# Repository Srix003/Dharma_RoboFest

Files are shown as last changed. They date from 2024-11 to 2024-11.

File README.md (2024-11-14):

# DHARMA BOT :dog2::robot:
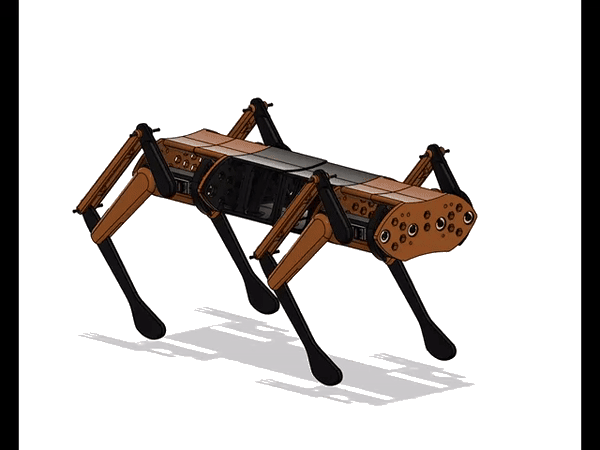
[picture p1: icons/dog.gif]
display_image


Dharma Bot is a sophisticated quadruped robotic dog featuring 12 degrees of freedom (DOF) for dynamic motion. The system includes a custom-designed remote control and smartwatch, which collectively offer seamless user interaction, control, and monitoring capabilities.

## Authors :writing_hand:

- [@mr-spaw](https://github.com/mr-spaw) :space_invader:
- [@LordCretivo](https://github.com/LordCretivo) :teddy_bear:
- [@DeepseaBandit](https://github.com/DeepseaBandit) :merman:

## Documentation :notebook_with_decorative_cover:

[Documentation](https://docs.google.com/document/d/14A3U6bSW9qBQt6sxEBGoiQTC8-wSntHT5azrs7TC3jw/edit?usp=sharing)

## System Overview :joystick: 
Dharma Bot is composed of three primary, electronically independent subsystems:
1. **The Bot**: The robotic dog, with core control and motion capabilities.
2. **Smart Remote**: The main control interface for the bot, featuring a Raspberry Pi, touchscreen, and long-range communication.
3. **Smartwatch**: A peripheral control and monitoring device equipped with sensors and ESP-32-based communications.
4. **Turret System**: The turret system is a rotating module mounted on the bot, designed to carry cameras and sensors. It provides 360-degree horizontal rotation and adjustable vertical tilt, enabling the bot to monitor or track targets in multiple directions.

## Subsystems

### [Smart Watch](Firmware/Utility_Watch/watch.md) :watch:
The smartwatch incorporates:
- **ESP-32 WROOM microcontroller**:The SoC of the embedded hardware.
- **OLED screen**: Displays real-time status, bot location, connectivity, and enemy detection data.
- **Pulse-meter sensor** and **GPS**: For monitoring the wearer's health and position.
- **Geotagging**: Logs location of deployed tags for tracking.
- **Heartbeat Monitoring**: In "Military Mode," it locks if the wearer’s pulse reads zero for over 30 seconds.
- **FailSafe Mechanism**: Notifies the remote of the current location upon triggering specific emergency conditions.
- **ESP-NOW Communication**: Provides secure data exchange between the smartwatch and the smart remote.

### Smart Remote  :video_game:
Serving as the primary control hub, the smart remote includes:
- **Raspberry Pi and 7-inch HDMI Touchscreen**: For intuitive control of the whole system architecture.
- **LoRa and ESP-NOW Modules**: Enabling long-range communication up to 10 km in LoRA and about five meters of communication with ESP-NOW protocol
- **GeoTag Integration**: Displays tagged locations on a map for rescue and tracking.
- **Video Streaming**: ESP-32 S3 CAM streaming for real-time surveillance.
- **Manual Controls**: Joysticks, potentiometers, and switches for bot locomotion and firing systems.
- **GUI**: The remote’s GUI interface provides a user-friendly experience, offering control over various modes, video feeds, and sensor data

### PoC Bot :dog2:
The main bot integrates:
- **Teensy 4.1 Microcontroller**: Manages core functions, including servo control and scheduling of Tasks
- **ESP 32 S3 Development Board**: Controlling the Peripheral Electronics like GPS, ToF Sensors and Gyroscopic Readngs.
- **MG99R Servo Motors**: 12 servo motors for precise locomotion.
- **ESP-32 S3 Camera System**: A esp camera system for live video feed.
- **LIDAR and GPS Modules**: For navigation and environmental awareness.
- **Communication**:  Local esp aceess network and long-range LoRa for data exchange between subsystems.

### Turret System :gun:
The turrent has:
- **Raspberry Pi**: Runs a local ML image recognition model and manages peripheral hardware.
- **ESP 32**: Controls the Servo motors

## Installation-Arduino IDE :computer:

### Ubuntu-linux64

Update Packages

```bash
sudo apt update
sudo apt upgrade
```

Installing Dependencies
```bash
sudo apt install -y wget unzip
```

Download the Arduino IDE
```bash
wget https://downloads.arduino.cc/arduino-<version>-linux64.tar.xz
```

Extract the Archive
```bash
tar -xf arduino-<version>-linux64.tar.xz
```

Install the Arduino IDE
```bash
cd arduino-<version>
sudo ./install.sh
```

Download the Arduino IDE
```bash
sudo usermod -aG dialout $USER
```

Launch Arduino IDE from Application menu or
[Arduino](https://www.arduino.cc/en/software)

then,
Go to File > Preferences (or Arduino > Preferences on macOS).
In the Preferences window, look for the field labeled Additional Board Manager URLs.
Paste the URLs for any additional board packages

```bash
http://arduino.esp8266.com/stable/package_esp8266com_index.json
https://github.com/earlephilhower/arduino-pico/releases/download/global/package_rp2040_index.json
https://raw.githubusercontent.com/espressif/arduino-esp32/gh-pages/package_esp32_index.json
https://www.pjrc.com/teensy/package_teensy_index.json
```
Go to Tools > Board > Board Manager.
Download ESP and Raspberry Pi Pico Board libraries
## 
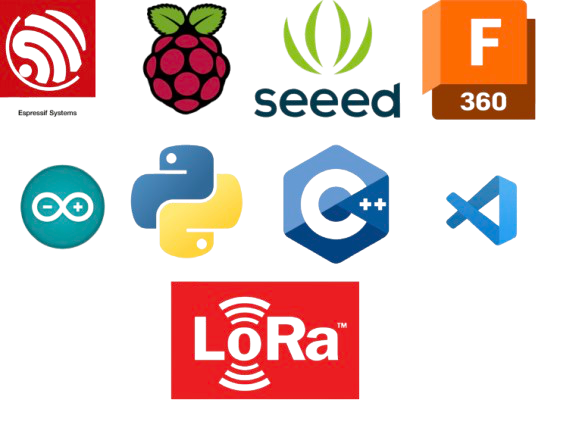
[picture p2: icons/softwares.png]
software_used


## Project Context :star: :india:
This project was developed as part of RoboFest, held in 2024, organised by Gujarat Council on Science and Technology(GUJCOST).

## Social Media :star2:
[Website](https://krs.kiit.ac.in)
[Instagram](https://www.instagram.com/kiit_robotics.society?utm_source=ig_web_button_share_sheet&igsh=ZDNlZDc0MzIxNw==)
[Linkedin](https://www.linkedin.com/company/kiit-robotics-society-bbsr/mycompany/)

## Project Link :link:
https://github.com/mr-spaw/Dharma_RoboFest

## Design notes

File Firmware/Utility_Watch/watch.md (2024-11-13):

# UTILITY WATCH :watch:

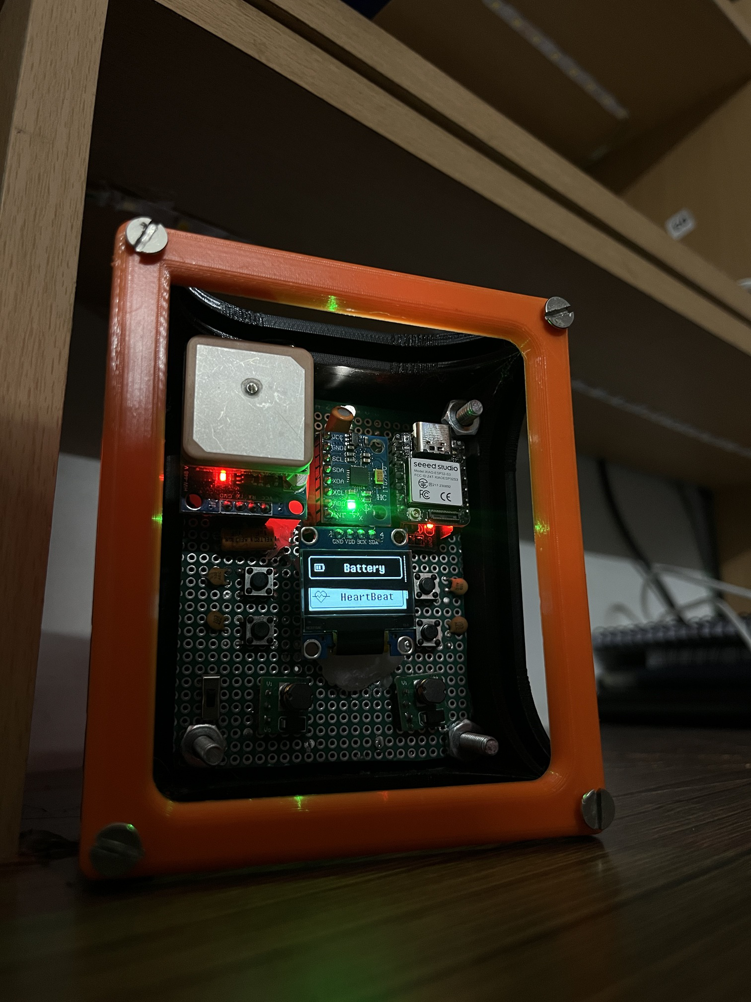
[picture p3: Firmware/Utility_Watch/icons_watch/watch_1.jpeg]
display_image


## Overview :eye_speech_bubble:

The Utility Watch is an embedded device designed to monitor health and environmental parameters using sensors. It includes features like heart rate monitoring, GPS tracking, and motion detection, with wireless data transmission through ESP-NOW. The watch has an OLED display for real-time data visualization and user interaction via buttons. In failsafe mode, if no motion or heart rate is detected, the watch disables user controls and only transmits essential data: heart rate and GPS location.

## Key Features :speech_balloon:

1. **Heart Rate Monitoring**: Utilizes the MAX30102 sensor to measure heart rate and SpO2 levels.

2. **GPS Tracking**: Retrieves geographical coordinates and satellite information using a GPS module.

3. **Motion Detection**: Employs the MPU6050 sensor to monitor motion and orientation.

4. **User Interface**: An OLED display provides graphical and textual feedback.
Users can navigate through different modes using buttons (up, down, select, and press).

5. **Failsafe Mode**: Activates when no motion or heart rate is detected. In this mode, the watch deactivates non-essential functions, rendering the buttons inactive. Only critical data, such as heart rate vitals and GPS location, is transmitted wirelessly.

## Components :play_or_pause_button:
**Microcontroller**: SEEDSTUDIO ESP32 S3

### Communication
ESP-NOW for wireless data transmission

### Sensors
1. **MPU6050**: Accelerometer and Gyroscope

2. **MAX30102**: Pulse Oximeter and Heart Rate Sensor

3. **NEO-7M**: Serial communication for location tracking

4. **OLED 0.96inch Display**: To dislplay the GUI of the watch

## RTOS Task Scheduling  :grey_exclamation:

### Task Breakdown

1. **Hardware Interrupts**: Handles button presses for user interaction.

2. **Sensor Data Acquisition**: Reads data from the MPU6050, MAX30102, and GPS.

3. **Data Preparation ESP-NOW**: Formats sensor data into a string for transmission.

4. **Data Transmission ESP-NOW**: Sends prepared data using ESP-NOW.

5. **OLED GUI Handling**: Updates the display based on user inputs and sensor readings.

6. **Data Retrieval ESP-NOW**: A preemptive task to manage background operations.

7. **FailSafe Mechanism**: Monitors sensor stability and activates failsafe mode if necessary.

8. **FailSafe GUI**: Displays relevant information during failsafe mode.

## Dependencies
To deploy this project run

```bash
Wire.h
Adafruit_GFX.h
Adafruit_SSD1306.h
MPU6050.h
esp_now.h
WiFi.h
SoftwareSerial.h
TinyGPS.h
MAX30105.h
heartRate.h
```
## Pin Configuration :part_alternation_mark:

The Smart Utility Watch utilizes various sensors and components, each connected to specific pins on the ESP32 microcontroller. Below is the detailed pin configuration for each component:

### GPS Module
```bash
Vcc: Connect to 3.3V
Gnd: Connect to Ground
Tx: Connect to Digital Pin D3
Rx: Connect to Digital Pin D2
```

### MAX30102 (Heart Rate Sensor)
```bash
Vcc: Connect to 3.3V
Gnd: Connect to Ground
SDA: Connect to Digital Pin D4
SCL: Connect to Digital Pin D5
```

### MPU6050 (Accelerometer and Gyroscope)
```bash
Vcc: Connect to 3.3V
Gnd: Connect to Ground
SDA: Connect to Digital Pin D4
SCL: Connect to Digital Pin D5
```

### OLED Display (SSD1306)
```bash
Vcc: Connect to 3.3V
Gnd: Connect to Ground
SDA: Connect to Digital Pin D4
SCL: Connect to Digital Pin D5
```

### Buttons
```bash
Up Button: Connect to Digital Pin D10
Down Button: Connect to Digital Pin D9
Select Button: Connect to Digital Pin D8
Press Button: Connect to Digital Pin D0
```

### Voltage Divider for ADC
```bash
R1: 10K Ohm resistor
R2: 1K Ohm resistor
ADC: Connect to Digital Pin D1
```
#### Notes

1. Ensure that all components are connected correctly to prevent damage to the sensors or the microcontroller.
2. The power supply should be stable 3.3V to the ESP32 and provide sufficient current for all connected devices.
3. Decoupling Capacitor is necessary for the button to ensure reliable operation.

## GUI :open_file_folder:
The smartwatch begins by detecting the wrist; if no wrist is detected, it will not proceed. Once detected, it starts collecting data, and when the heartbeat exceeds 30 BPM, it transitions to the main interface. The most recent GPS, MPU, and heart rate data are stored in a linked list with the newest entry at the top and the oldest at the bottom.

The main interface has four sections. 

The main interface is divided into four sections:

1. **Enemy Section**: Displays the watch’s mode and the remote dog's mode—Sentry mode, Scout mode, and Follow mode—and shows any enemy detected by the bot.
2. **GPS Section**: Shows the device's current latitude, longitude, and the number of connected satellites.
3. **Battery Section**: Indicates the battery levels of the smartwatch, the remote, and the POC bot.
4. **Heart Vitals Section**: Displays the user’s current BPM and average BPM readings.

### Failsafe Mechanism
The FailSafe Mechanism, begins by collecting pitch, roll, and yaw values from the first node, then compares these values to nodes 2 through 5 to check for stability within a defined tolerance. If all nodes are stable and the average BPM of the first node is below 25, it activates the failsafe mode. This triggers specific safety actions, such as calling task3 and task4 and setting a failsafe_bool flag to indicate that failsafe mode is active.

## Conclusion

The Smart Utility Watch is a versatile device that combines health monitoring and GPS functionalities in a compact form factor. Its modular design allows for easy updates and improvements, making it a suitable project for both hobbyists and developers interested in wearable technology.

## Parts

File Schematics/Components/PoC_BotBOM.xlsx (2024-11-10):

Components | Quantity | Price | Total Price | Link
Teensy 4.1 Dev-Board | 1 | 2658 | 2658 | https://robu.in/product/buy-teensy-4-1-development-board/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
ESP 32 S3 Dev-Board | 1 | 1388 | 1388 | https://robu.in/product/smartelex-esp32-s3-development-kit-m-1-1-pcs/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
Seedstudio XIAO ESP-S3 Cam | 1 | 1300 | 1300 | https://www.digikey.in/en/products/detail/seeed-technology-co.,-ltd/113991115/18724504?cur=INR&lang=en&gad_source=1&gbraid=0AAAAADrbLlhHJjHy-7D3tAoVhXMwgyvdG
SX1278 LoRa Module | 1 | 430 | 430 | https://robocraze.com/products/sx1278-lora-module-ra-02-433mhz-wireless-spread-spectrum-transmission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
GY-91 10 DOF IMU MPU-9250 with BMP280 | 1 | 590 | 590 | https://robu.in/product/gy-91-mpu9250bmp280-10dof-acceleration-gyro-9-axis-sensor-module/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
VL53LoX ToF Sensor | 4 | 111 | 444 | https://robu.in/product/vl53l0x-tof-based-lidar-laser-distance-sensor/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
NEO 7M GPS Module | 1 | 545 | 545 | https://robu.in/product/neo-7m-000-neo-7m-gps-module-mwc-gy-neo-7m-v2-flight-control-gps-module-eeprom-mwc-apm2-5/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
1.3 inch OLED Display | 1 | 350 | 350 | https://zbotic.in/product/1-3-inch-i2c-iic-4-pin-oled-display-module-with-vcc-gnd-blue/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
MG996R Servo Motor | 12 | 309 | 3708 | https://robu.in/product/towerpro-mg995-servo-high-speed-digital-metal-gear-ball-bearing-torque-12kg-robot-arduino-good-quality180-degree-rotation/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
AMS1117 3.3V Module | 3 | 18 | 54 | https://robu.in/product/ams1117-3-3-ldo-800ma-dc-5v-3-3v-step-power-supply-module/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
USB Buck Converter | 2 | 80 | 160 | https://robu.in/product/usb-fast-charging-module/?gad_source=1&gbraid=0AAAAADvLFWfHbZ1aIqX8F5rfsQEMRjSHD
XT-60 Connector | 2 | 26 | 52 | https://robocraze.com/products/xt60-connector-pair?currency=INR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
4s Battery | 1 | 1869 | 1869 | https://robu.in/product/orange-2200mah-4s-40c80c-lithium-polymer-battery-pack-lipo/
VeroBoard | 6 | 94 | 564 | https://robu.in/product/10-x-15-cm-universal-pcb-prototype-board-single-sided-2-54mm-hole-pitch/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
Silicon Wire 18 AWG | 4 | 60 | 240 | https://robu.in/product/high-quality-ultra-flexible-18awg-silicone-wire-red/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
JST-XT connectors 2 pin | 10 | 60 | 600 | https://robu.in/product/2-pin-jst-xh-2-54mm-pitch-plug-and-socket-with-cable-10-pcs/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
JST-XT connectors 4 pin | 15 | 50 | 750 | https://zbotic.in/product/6-pin-jst-xh-2-54mm-pitch-plug-and-socket-with-cable-3-pcs/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
PCT-SPL 2:6 | 2 | 66 | 132 | https://robu.in/product/pct-spl-62-0-08-2-5mm-62-pole-wire-connector-terminal-block-with-spring-lock-lever-for-cable-connection/
PCT-SPL 1:1 | 2 | 21 | 42 | https://robu.in/product/lt-211spl-1-quick-connection-terminals-can-be-spliced/
Silicon Wire 28 AWG | 4 | 60 | 240 | https://robu.in/product/28awg-silicone-wire/?gad_source=1&gbraid=0AAAAADvLFWeTgUz2OswCMdNMzaCTK1-p6
Total |  |  | 16116

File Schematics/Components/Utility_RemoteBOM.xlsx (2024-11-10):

Component | Quantity | Price | Total | Link
70H-1024600-IPS-Panel by Waveshare | 1 | 4649 | 4649.00 | https://thinkrobotics.com/products/7inch-qled-integrated-touch-display-1024-600?variant=46572922995005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
Raspberry Pi 5 4 GB | 1 | 5799 | 5799.00 | https://robu.in/product/raspberry-pi-5-model-4gb/
ESP 32 S3 Dev-Boards | 2 | 1388 | 2776.00 | https://robu.in/product/smartelex-esp32-s3-development-kit-m-1-1-pcs/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
ESP 32 Dev-Board | 1 | 420 | 420.00 | https://robocraze.com/products/nodemcu-32-wifi-bluetooth-esp32-development-board30-pin?variant=42268194046176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
SX1278 LoRa Module | 1 | 430 | 430.00 | https://robocraze.com/products/sx1278-lora-module-ra-02-433mhz-wireless-spread-spectrum-transmission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
3.7v Lithium Ion Batterys | 6 | 149 | 894.00 | https://robu.in/product/orange-icr-18650-2200mah-lithium-ion-battery/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
4s BMS Module | 1 | 160 | 160.00 | https://robu.in/product/4s-20a-lithium-battery-protection-board/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
4s Charger Module | 1 | 260 | 260.00 | https://robu.in/product/18650-polymer-lithium-ion-charger-type-c-to-4s-16-8v-4a-booster-module/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
AMS1117 3.3V modules | 3 | 18 | 54.00 | https://robu.in/product/ams1117-3-3-ldo-800ma-dc-5v-3-3v-step-power-supply-module/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
USB Buck converters 5V | 2 | 80 | 160.00 | https://robu.in/product/usb-fast-charging-module/?gad_source=1&gbraid=0AAAAADvLFWfHbZ1aIqX8F5rfsQEMRjSHD
2-axis Joysticks | 4 | 44 | 176.00 | https://robocraze.com/products/joystick-module?variant=40192421527705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
Switch | 2 | 16 | 32.00 | https://evelta.com/rocker-switch-on-off-spst-2pin-black-button-black-housing-kcd1-2-101/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
Toggle Switch | 3 | 30 | 90.00 | https://robu.in/product/smts-102-sub-miniature-toggle-switch-3pinon-on/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
Veroboard | 6 | 94 | 564.00 | https://robu.in/product/10-x-15-cm-universal-pcb-prototype-board-single-sided-2-54mm-hole-pitch/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
Silicon Wire 28 AWG | 6 | 60 | 360.00 | https://robu.in/product/28awg-silicone-wire/?gad_source=1&gbraid=0AAAAADvLFWeTgUz2OswCMdNMzaCTK1-p6
PCB power terminal | 15 | 10 | 150.00 | https://robu.in/product/2-pin-straight-pcb-screw-terminal-block-connector-3-5mm-pitch/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
5v Buck Converter | 2 | 100 | 200.00 | https://robu.in/product/ultra-small-size-dc-dc-5v-3a-bec-power-supply-buck-step-down-module/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
18650 Battery Holder | 5 | 83 | 415.00 | https://robu.in/product/18650-dual-smd-smt-high-quality-single-battery-holder/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
Silicon Wire 18 AWG | 3 | 60 | 180.00 | https://robu.in/product/high-quality-ultra-flexible-18awg-silicone-wire-red/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
JST-XT connectors 2 pin | 10 | 60 | 600.00 | https://robu.in/product/2-pin-jst-xh-2-54mm-pitch-plug-and-socket-with-cable-10-pcs/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
JST-XT connectors 4 pin | 30 | 50 | 1500.00 | https://zbotic.in/product/6-pin-jst-xh-2-54mm-pitch-plug-and-socket-with-cable-3-pcs/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
PCT-SPL 2:6 | 2 | 66 | 132.00 | https://robu.in/product/pct-spl-62-0-08-2-5mm-62-pole-wire-connector-terminal-block-with-spring-lock-lever-for-cable-connection/
PCT-SPL 1:1 | 4 | 21 | 84.00 | https://robu.in/product/lt-211spl-1-quick-connection-terminals-can-be-spliced/
5V to 3.3 Buck converter | 1 | 90 | 90.00 | https://robu.in/product/dc-dc-3a-5v-12v-24v-to-3-3v-step-down-power-supply-module/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
Total |  |  | 20175.00

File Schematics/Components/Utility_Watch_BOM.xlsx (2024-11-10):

Components | Quantity | PRICE | TOTAL | Link
GPS NEO 7M | 1 | 545 | 545 | https://robu.in/product/neo-7m-000-neo-7m-gps-module-mwc-gy-neo-7m-v2-flight-control-gps-module-eeprom-mwc-apm2-5/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
Seedstudio XIAO ESP S3 | 1 | 686 | 686 | https://robu.in/product/seeed-studio-xiao-esp32s3-2-4ghz-wifi-ble-5-0/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
MPU 6050 | 1 | 140 | 140 | https://robocraze.com/products/mpu-6050-triple-axis-accelerometer-gyroscope-module?variant=40192322011289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
0.96 inch OLED Screen | 1 | 140 | 140 | https://robocraze.com/products/0-96in-oled-display?variant=40192586645657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
Tactile buttons(pack of 20) | 1 | 59 | 59 | https://robu.in/product/6x6x5mm-tactile-push-button-switch-pack-of-20/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
TP4056 charging module | 1 | 17 | 17 | https://zbotic.in/product/tp4056-battery-charging-protection-module-type-c/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
3.7v Lithium Ion Battery | 1 | 200 | 200 | https://robu.in/product/450mah-pcm-protected-micro-li-po-battery/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
Vero Board | 1 | 85 | 85 | https://robu.in/product/9-x-15-cm-universal-pcb-prototype-board-single-sided-2-54mm-hole-pitch/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
3.3V to 5V boost converter | 2 | 48 | 96 | https://www.flyrobo.in/1.5v-1.8v-2.5v-3v-3.3v-3.7v-4.2v-5v-dc-dc-dc-boost-converter-step-up-module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
AMS1117 LDO | 2 | 18 | 36 | https://robu.in/product/ams1117-3-3-ldo-800ma-dc-5v-3-3v-step-power-supply-module/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
Silicon Wire 28 AWG | 2 | 60 | 120 | https://robu.in/product/28awg-silicone-wire/?gad_source=1&gbraid=0AAAAADvLFWeTgUz2OswCMdNMzaCTK1-p6
TOTAL |  |  | 2004

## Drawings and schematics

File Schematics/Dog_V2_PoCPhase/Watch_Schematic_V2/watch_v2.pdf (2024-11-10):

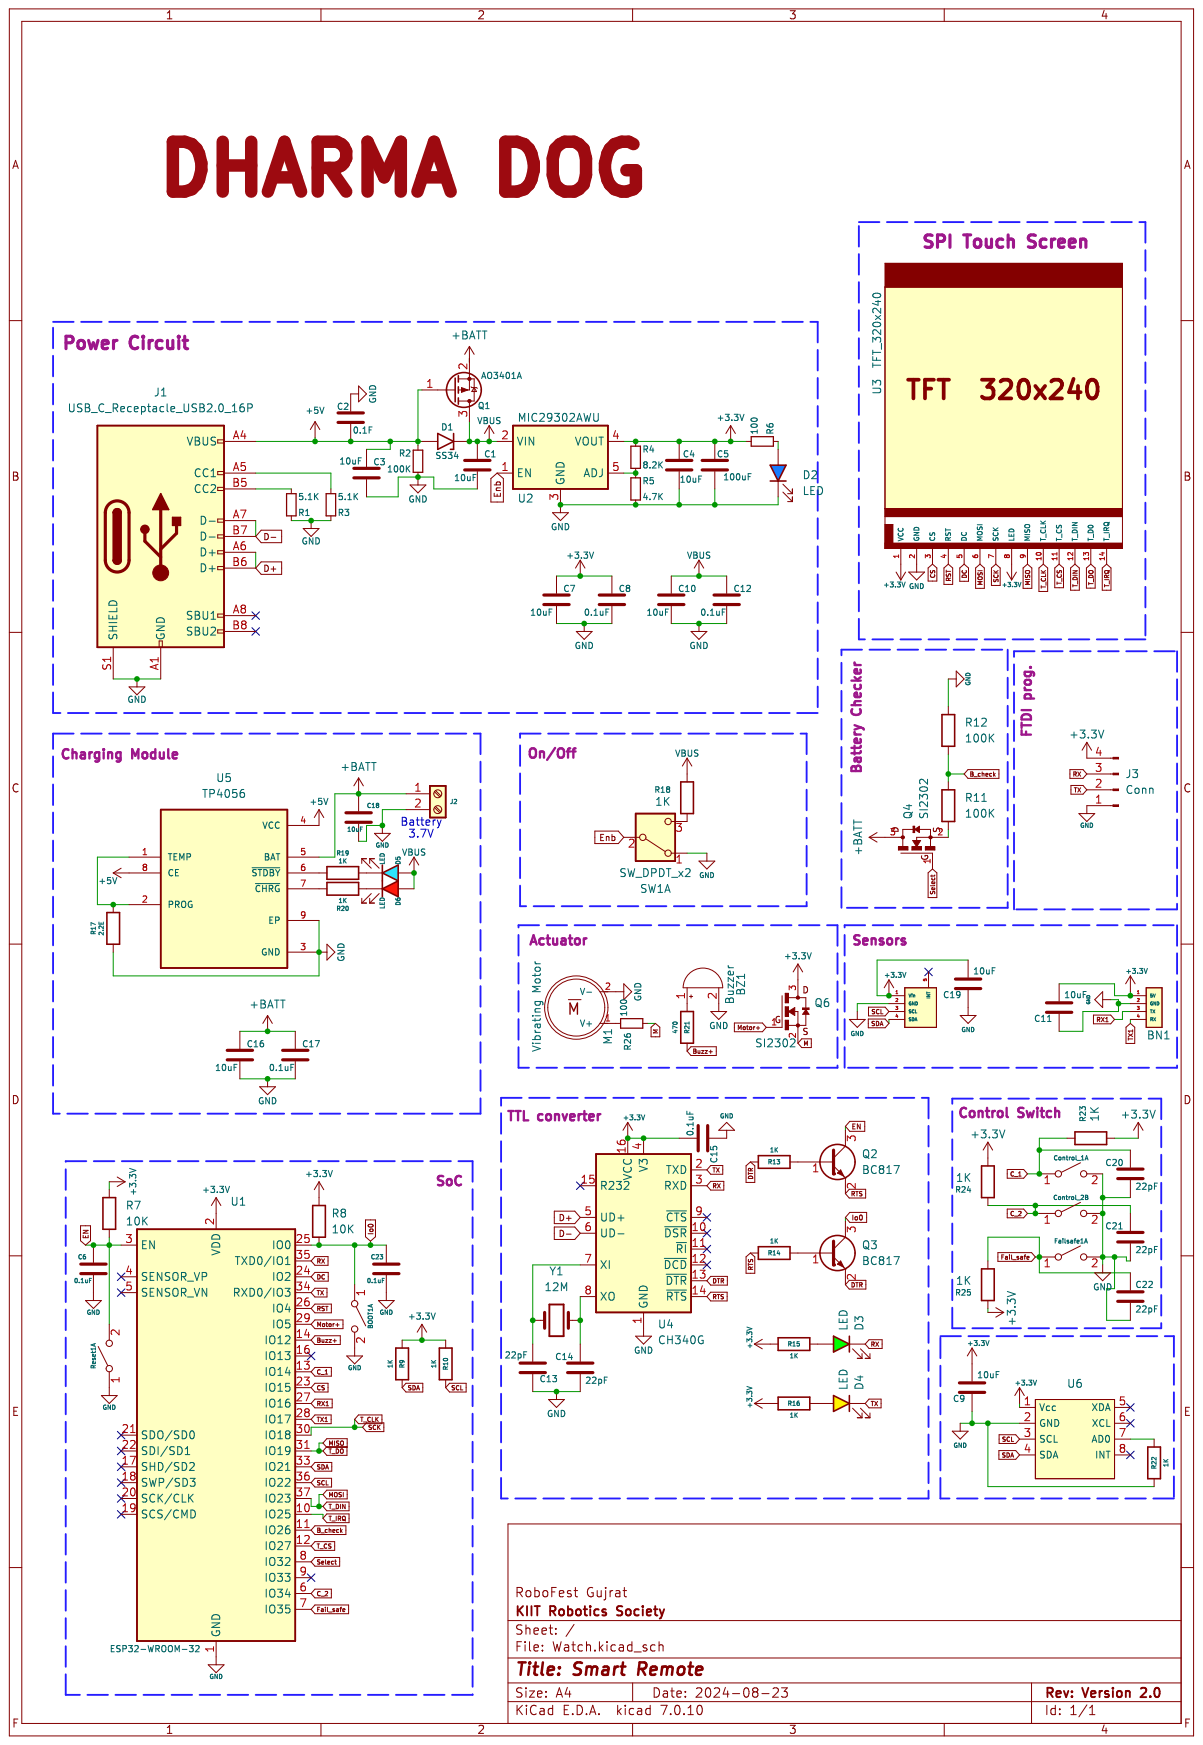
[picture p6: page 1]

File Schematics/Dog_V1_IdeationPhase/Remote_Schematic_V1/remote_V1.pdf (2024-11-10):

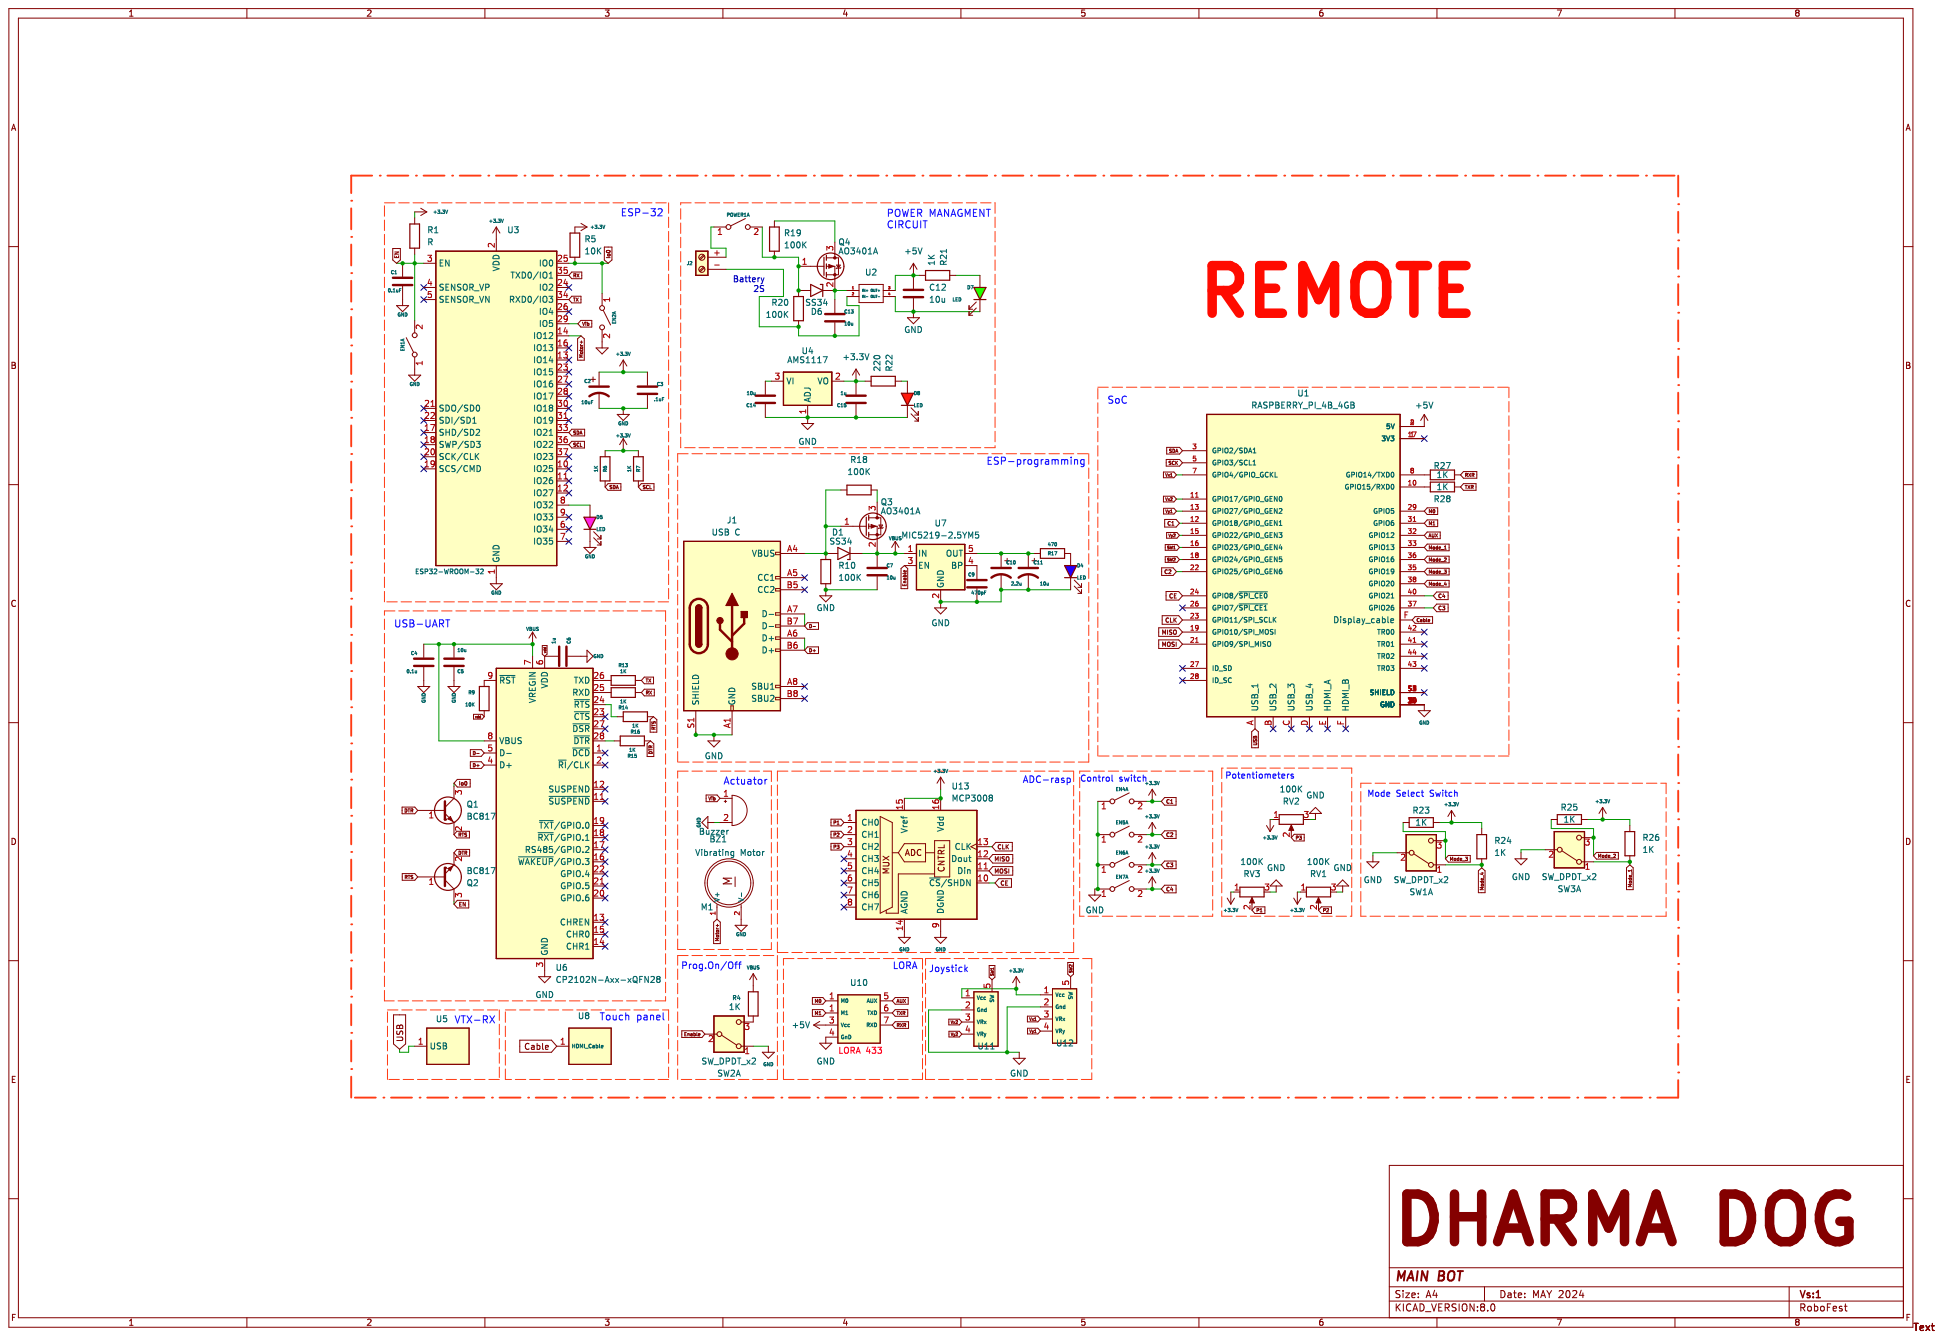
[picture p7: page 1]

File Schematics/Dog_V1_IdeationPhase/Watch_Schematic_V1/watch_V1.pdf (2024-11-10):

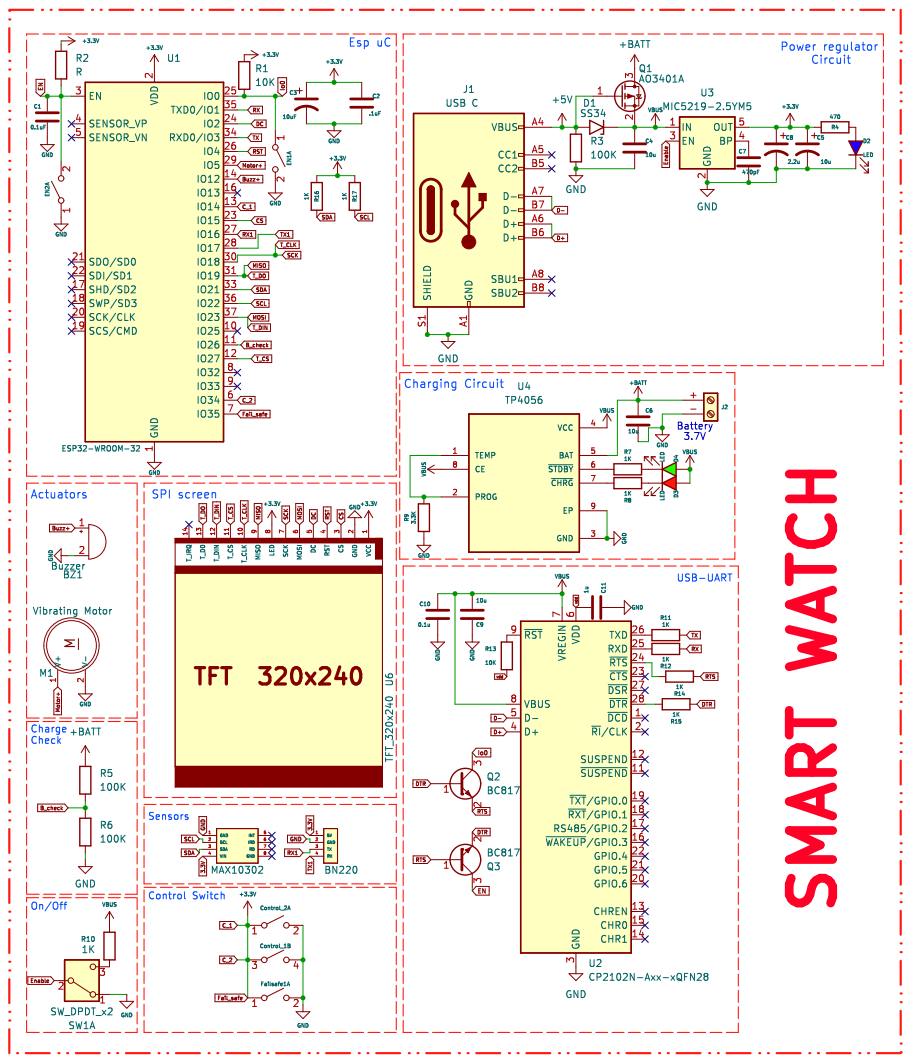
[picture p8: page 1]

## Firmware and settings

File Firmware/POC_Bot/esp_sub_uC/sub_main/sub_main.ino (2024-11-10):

#include <Wire.h>
#include <Adafruit_GFX.h>
#include <Adafruit_SH110X.h>
#include <SoftwareSerial.h> //softserail for UART
#include <TinyGPS.h>
#include <Adafruit_VL53L0X.h>
#include <MPU9250_asukiaaa.h>
#include <Adafruit_BMP280.h>
#include <freertos/FreeRTOS.h>
#include <freertos/task.h>
#include <freertos/semphr.h>

SemaphoreHandle_t xSemaphore;

#ifdef _ESP32_HAL_I2C_H_
#define SDA_PIN 6
#define SCL_PIN 7
#endif

#define i2c_Address 0x3c 
#define SLAVE_ADDR 0x78 
SoftwareSerial mySerial(41, 42);

#define SCREEN_WIDTH 128 
#define SCREEN_HEIGHT 64 
#define OLED_RESET -1
Adafruit_SH1106G display = Adafruit_SH1106G(SCREEN_WIDTH, SCREEN_HEIGHT, &Wire, OLED_RESET);


TinyGPS gps;

Adafruit_BMP280 bme;
MPU9250_asukiaaa mySensor;

float aX, aY, aZ, aSqrt, gX, gY, gZ;
float latitude, longitude;
int distance_sensor1;
int distance_sensor2;
int distance_sensor3;
int distance_sensor4;
String dist="";
int tol=100;


#define SENSOR1_WIRE Wire
#define SENSOR2_WIRE Wire
#define SENSOR3_WIRE Wire
#define SENSOR4_WIRE Wire

// Setup mode for doing reads
typedef enum {
  RUN_MODE_DEFAULT = 1,
  RUN_MODE_CONT
} runmode_t;

runmode_t run_mode = RUN_MODE_DEFAULT;
uint8_t show_command_list = 1;

typedef struct {
  Adafruit_VL53L0X *psensor; // pointer to object
  TwoWire *pwire;
  int id;            // id for the sensor
  int shutdown_pin;  // which pin for shutdown;
  Adafruit_VL53L0X::VL53L0X_Sense_config_t
      sensor_config;     // options for how to use the sensor
  uint16_t range;        // range value used in continuous mode stuff.
  uint8_t sensor_status; // status from last ranging in continuous.
} sensorList_t;

// Actual object, could probably include in structure above61
Adafruit_VL53L0X sensor1;
Adafruit_VL53L0X sensor2;
Adafruit_VL53L0X sensor3;
Adafruit_VL53L0X sensor4;

// Setup for 4 sensors
sensorList_t sensors[] = {
    {&sensor1, &SENSOR1_WIRE, 0x30, 10,
     Adafruit_VL53L0X::VL53L0X_SENSE_LONG_RANGE, 0, 0},
    {&sensor2, &SENSOR2_WIRE, 0x31, 11,
     Adafruit_VL53L0X::VL53L0X_SENSE_HIGH_SPEED, 0, 0},
    {&sensor3, &SENSOR3_WIRE, 0x32, 12,
     Adafruit_VL53L0X::VL53L0X_SENSE_DEFAULT, 0, 0},
    {&sensor4, &SENSOR4_WIRE, 0x33, 13,
     Adafruit_VL53L0X::VL53L0X_SENSE_DEFAULT, 0, 0}
};

const int COUNT_SENSORS = sizeof(sensors) / sizeof(sensors[0]);

const uint16_t ALL_SENSORS_PENDING = ((1 << COUNT_SENSORS) - 1);
uint16_t sensors_pending = ALL_SENSORS_PENDING;
uint32_t sensor_last_cycle_time;


void Initialize_sensors() {
  bool found_any_sensors = false;
  // Set all shutdown pins low to shutdown sensors
  for (int i = 0; i < COUNT_SENSORS; i++)
    digitalWrite(sensors[i].shutdown_pin, LOW);
  delay(10);

  for (int i = 0; i < COUNT_SENSORS; i++) {
    // one by one enable sensors and set their ID
    digitalWrite(sensors[i].shutdown_pin, HIGH);
    delay(10); // give time to wake up.
    if (sensors[i].psensor->begin(sensors[i].id, false, sensors[i].pwire,
                                  sensors[i].sensor_config)) {
      found_any_sensors = true;
    } else {
      Serial.print(i, DEC);
      Serial.print(F(": failed to start\n"));
    }
  }
  if (!found_any_sensors) {
    Serial.println("No valid sensors found");
    while (1)
      ;
  }
}
//====================================================================
// Simple Sync read sensors.
//====================================================================
void read_sensors() {
  // First use simple function
  uint16_t ranges_mm[COUNT_SENSORS];
  bool timeouts[COUNT_SENSORS];
  uint32_t stop_times[COUNT_SENSORS];

  digitalWrite(13, HIGH);
  uint32_t start_time = millis();
  for (int i = 0; i < COUNT_SENSORS; i++) {
    ranges_mm[i] = sensors[i].psensor->readRange();
    timeouts[i] = sensors[i].psensor->timeoutOccurred();
    stop_times[i] = millis();
  }
  uint32_t delta_time = millis() - start_time;
  digitalWrite(13, LOW);

  Serial.print(delta_time, DEC);
  Serial.print(F(" "));
  for (int i = 0; i < COUNT_SENSORS; i++) {
    Serial.print(i, DEC);
    Serial.print(F(":"));
    Serial.print(ranges_mm[i], DEC);
    Serial.print(F(" "));
    Serial.print(stop_times[i] - start_time, DEC);
    if (timeouts[i])
      Serial.print(F("(TIMEOUT) "));
    else
      Serial.print(F("          "));
    start_time = stop_times[i];
  }
  Serial.println();
}

//===============================================================
// Continuous range test code
//===============================================================

void start_continuous_range(uint16_t cycle_time) {
  if (cycle_time == 0)
    cycle_time = 100;
  Serial.print(F("start Continuous range mode cycle time: "));
  Serial.println(cycle_time, DEC);
  for (uint8_t i = 0; i < COUNT_SENSORS; i++) {
    sensors[i].psensor->startRangeContinuous(cycle_time); // do 100ms cycle
  }
  sensors_pending = ALL_SENSORS_PENDING;
  sensor_last_cycle_time = millis();
}

void stop_continuous_range() {
  Serial.println(F("Stop Continuous range mode"));
  for (uint8_t i = 0; i < COUNT_SENSORS; i++) {
    sensors[i].psensor->stopRangeContinuous();
  }
  delay(100); // give time for it to complete.
}

void Process_continuous_range() {

  uint16_t mask = 1;
  for (uint8_t i = 0; i < COUNT_SENSORS; i++) {
    bool range_complete = false;
    if (sensors_pending & mask) {
      if (range_complete) {
        sensors[i].range = sensors[i].psensor->readRangeResult();
        sensors[i].sensor_status = sensors[i].psensor->readRangeStatus();
        sensors_pending ^= mask;
      }
    }
    mask <<= 1; // setup to test next one
  }
  // See if we have all of our sensors read OK
  uint32_t delta_time = millis() - sensor_last_cycle_time;
  if (!sensors_pending || (delta_time > 1000)) {
    digitalWrite(13, !digitalRead(13));
    Serial.print(delta_time, DEC);
    Serial.print(F("("));
    Serial.print(sensors_pending, HEX);
    Serial.print(F(")"));
    mask = 1;
    for (uint8_t i = 0; i < COUNT_SENSORS; i++) {
      Serial.print(F(" : "));
      if (sensors_pending & mask)
        Serial.print(F("TTT")); // show timeout in this one
      else {
        Serial.print(sensors[i].range, DEC);
        if (sensors[i].sensor_status == VL53L0X_ERROR_NONE)
          Serial.print(F("  "));
        else {
          Serial.print(F("#"));
          Serial.print(sensors[i].sensor_status, DEC);
        }
      }
    }
    // setup for next pass
    Serial.println();
    sensor_last_cycle_time = millis();
    sensors_pending = ALL_SENSORS_PENDING;
  }
}

void requestEvent() {
  vTaskSuspendAll();
String response = String("x") + "," + String(aX) + "," +
                 String(aY) + "," +
                 String(aZ) + "," +
                 String(gX) + "," +
                 String(gY) + "," +
                 String(gZ) + "," +
                 String(latitude) + "," + 
                 String(longitude) + "," +
                 String(dist) + "," +
                 String(distance_sensor1) +"," +
                 String(distance_sensor2) +"," +
                 String(distance_sensor3) +"," +
                 String(distance_sensor4) +"," + String("y");


    byte responseData[response.length() + 1];
    response.toCharArray((char*)responseData, response.length() + 1);
    Wire1.write(responseData, response.length() + 1);
    xTaskResumeAll();
}

// Task to read accelerometer data
void taskReadAccel(void *pvParameters) {
  while (true) {
    if (mySensor.accelUpdate() == 0) {
      aX = mySensor.accelX();
      aY = mySensor.accelY();
      aZ = mySensor.accelZ();
      aSqrt = mySensor.accelSqrt();
      
      Serial.print("Accel -> X: " + String(aX) + " Y: " + String(aY) + " Z: " + String(aZ) + " Sqrt: " + String(aSqrt) + "\t");
    }
    vTaskDelay(100 / portTICK_PERIOD_MS); // Delay to allow other tasks to run
  }
}

// Task to read gyroscope data
void taskReadGyro(void *pvParameters) {
  while (true) {
    if (mySensor.gyroUpdate() == 0) {
      gX = mySensor.gyroX();
      gY = mySensor.gyroY();
      gZ = mySensor.gyroZ();
      Serial.print("Gyro -> X: " + String(gX) + " Y: " + String(gY) + " Z: " + String(gZ) + "\t");
    }
    vTaskDelay(100 / portTICK_PERIOD_MS);
  }
}

void taskOLED(void *pvParameters) {

  while(true){
  display.setTextSize(1);
  display.setTextColor(SH110X_WHITE);
  display.setCursor(0, 0);
  display.println("We will win");
  display.display();
  
  vTaskDelay(500 / portTICK_PERIOD_MS);
   
}
}

void taskGPS(void *pvParameters) {
  while (true) {
    bool newData = false;
    unsigned long chars;
    unsigned short sentences, failed;

    // For one second, read data from GPS
    while (mySerial.available() > 0) {
      gps.encode(mySerial.read());
      newData = true;
    }

    if (newData) {
     
      gps.f_get_position(&latitude, &longitude);
      Serial.print("Latitude: "); Serial.println(latitude, 6);
      Serial.print("Longitude: "); Serial.println(longitude, 6);
      
    }
    
    vTaskDelay(1000 / portTICK_PERIOD_MS); // Delay to prevent flooding
  }
}


void taskToF(void *pvParameters){
  while (1) {
    if (sensors[0].psensor != nullptr) {
      distance_sensor1 = sensors[0].psensor->readRange();
      Serial.print("1: ");
      Serial.println(distance_sensor1);
    } else {
      Serial.println("Sensor 1 not initialized");
    }

    vTaskDelay(10 / portTICK_PERIOD_MS);  // Delay between sensor readings

    if (sensors[1].psensor != nullptr) {
      distance_sensor2 = sensors[1].psensor->readRange();
      Serial.print("2: ");
      Serial.println(distance_sensor2);
    } else {
      Serial.println("Sensor 2 not initialized");
    }

    vTaskDelay(10 / portTICK_PERIOD_MS);

    if (sensors[2].psensor != nullptr) {
      distance_sensor3 = sensors[2].psensor->readRange();
      Serial.print("3: ");
      Serial.println(distance_sensor3);
    } else {
      Serial.println("Sensor 3 not initialized");
    }

    vTaskDelay(10 / portTICK_PERIOD_MS);

    if (sensors[3].psensor != nullptr) {
      distance_sensor4 = sensors[3].psensor->readRange();
      Serial.print("4: ");
      Serial.println(distance_sensor4);
    } else {
      Serial.println("Sensor 4 not initialized");
    }
    vTaskDelay(1000 / portTICK_PERIOD_MS);  // Delay between cycles
  }
}





void setup() {
  Serial.begin(115200);
  mySerial.begin(9600);
  while (!Serial);

  Wire.begin(SDA_PIN, SCL_PIN);

  Wire1.begin(SLAVE_ADDR,4,5,400000); //I2C slave
  Wire1.onRequest(requestEvent);

#ifdef _ESP32_HAL_I2C_H_
  Wire.begin(SDA_PIN, SCL_PIN);
  mySensor.setWire(&Wire);
#else
  Wire.begin();
  mySensor.setWire(&Wire);
#endif

  mySensor.beginAccel();
  mySensor.beginGyro();

  Serial.println("ESP32 I2C Slave Ready...");

  delay(250);
  display.begin(i2c_Address, true); //OLED display
  display.display();
  delay(2000);
  display.clearDisplay();
  delay(2000);

    // initialize all of the pins.
  Serial.println(F("VL53LOX_multi start, initialize IO pins"));
  
  for (int i = 0; i < COUNT_SENSORS; i++) { //ToF sensor
    pinMode(sensors[i].shutdown_pin, OUTPUT);
    digitalWrite(sensors[i].shutdown_pin, LOW);
  }
  Serial.println(F("Starting..."));
  Initialize_sensors();

    xSemaphore = xSemaphoreCreateMutex();

  // Create RTOS tasks for each sensor
  xTaskCreatePinnedToCore(taskReadAccel, "ReadAccel", 2048, NULL, 1, NULL, tskNO_AFFINITY);
  xTaskCreatePinnedToCore(taskReadGyro, "ReadGyro", 2048, NULL, 1, NULL, tskNO_AFFINITY);

  xTaskCreatePinnedToCore(taskOLED, "OLEDTASK", 2048, NULL, 2, NULL, tskNO_AFFINITY);
  xTaskCreatePinnedToCore(taskGPS, "OLEDGPS", 2048, NULL, 2, NULL, tskNO_AFFINITY);
  xTaskCreatePinnedToCore(taskToF, "TOF", 2048, NULL, 3, NULL, tskNO_AFFINITY);

}


void loop() {
  // Empty loop as all tasks run independently
}

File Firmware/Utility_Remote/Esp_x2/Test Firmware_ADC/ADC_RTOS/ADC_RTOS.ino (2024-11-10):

/*

----------------------------------------------------------------
Task 1->reading all the analog values and updating the values
----------------------------------------------------------------
Task 2->setting the mode according to the values
----------------------------------------------------------------
Task 3->Sending the modes by I2C
----------------------------------------------------------------

Joystick 1
X Axis->GPIO 4: 
Y Axis->GPIO 5


Joystick 2
X Axis->GPIO 6
Y Axis->GPIO 7


Joystick 3
X Axis->GPIO 8
Y Axis->GPIO 3


Joystick 4
X Axis->GPIO 9
Y Axis->GPIO 10

----------------------------------------------------------------
Mode Set

Sentri->37
Scout->36
Follow->35
----------------------------------------------------------------

Highest Limit ADC=4000
Lowest Limit ADC=30

*/

#include <Wire.h>
#include <freertos/FreeRTOS.h>
#include <freertos/task.h>

#define ADC_HIGH 4000
#define ADC_LOW 30
#define J1X 4
#define J1Y 5
#define J2X 6
#define J2Y 7
#define J3X 8
#define J3Y 3
#define J4X 9
#define J4Y 10
#define toggle1 37
#define toggle2 36
#define toggle3 35
#define LED 41

// Variable declaration
volatile bool mode_Centri = 0;
volatile bool mode_Scout = 0;
volatile bool mode_Follow = 0;

volatile int analogVal_J1X = 0;
volatile int analogVal_J1Y = 0;
volatile int analogVal_J2X = 0;
volatile int analogVal_J2Y = 0;
volatile int analogVal_J3X = 0;
volatile int analogVal_J3Y = 0;
volatile int analogVal_J4X = 0;
volatile int analogVal_J4Y = 0;


// Global variables to track the previous state of the modes
volatile bool prev_mode_Centri = false;  // Stores the previous state of mode_Centri
volatile bool prev_mode_Follow = false;    // Stores the previous state of mode_Flow
volatile bool prev_mode_Scout = false;   // Stores the previous state of mode_Scout

volatile bool mode_using=false;
volatile bool joystick_mode=false;

volatile bool prev_analogVal_J1X=false;
volatile bool prev_analogVal_J1Y=false;
volatile bool prev_analogVal_J2X=false;
volatile bool prev_analogVal_J2Y=false;
volatile bool prev_analogVal_J3X=false;
volatile bool prev_analogVal_J3Y=false;
volatile bool prev_analogVal_J4X=false;
volatile bool prev_analogVal_J4Y=false;


volatile bool joystick=0;
String mode="NULL";
String joystick_mode_sent="NULL";

const int val = 30;

TaskHandle_t Task1;
TaskHandle_t Task2;
TaskHandle_t Task3;
TaskHandle_t Task4;
TaskHandle_t Task5;

#define SLAVE_ADDR 0x08  // I2C address of ESP32 (Slave)

void readADC() {
    for (int i = 0; i <= val; i++) {
        analogVal_J1X = analogRead(J1X) + analogVal_J1X;
        analogVal_J1Y = analogRead(J1Y) + analogVal_J1Y;
        analogVal_J2X = analogRead(J2X) + analogVal_J2X;
        analogVal_J2Y = analogRead(J2Y) + analogVal_J2Y;
        analogVal_J3X = analogRead(J3X) + analogVal_J3X;
        analogVal_J3Y = analogRead(J3Y) + analogVal_J3Y;
        analogVal_J4X = analogRead(J4X) + analogVal_J4X;
        analogVal_J4Y = analogRead(J4Y) + analogVal_J4Y;
    }
}

void avgADCval() {
    analogVal_J1X = analogVal_J1X / val;
    analogVal_J1Y = analogVal_J1Y / val;
    analogVal_J2X = analogVal_J2X / val;
    analogVal_J2Y = analogVal_J2Y / val;
    analogVal_J3X = analogVal_J3X / val;
    analogVal_J3Y = analogVal_J3Y / val;
    analogVal_J4X = analogVal_J4X / val;
    analogVal_J4Y = analogVal_J4Y / val;
}

void readstate() {
    mode_Centri = digitalRead(toggle1);
    mode_Scout = digitalRead(toggle2);
    mode_Follow = digitalRead(toggle3);
}


//reading values
void task1(void *pvParameters) {
    while (1) {

        readADC();
        avgADCval();
        readstate();

        if(joystick_mode_sent=="NULL"){
          digitalWrite(LED,HIGH);
        }
        if(joystick_mode_sent!="NULL"){
          digitalWrite(LED,LOW);
        }
        vTaskDelay(100 / portTICK_PERIOD_MS);  // Delay to prevent watchdog
    }
}

//logic for Dog Mode
void task2(void *pvParameters) {
    while (1) {
     if(mode_Centri == false && prev_mode_Centri== false && mode_using==false ){
        mode="Centri";
        prev_mode_Centri=true;
        mode_using=true;
        }
      if(mode_Centri == true && prev_mode_Centri== true && mode_using==true){
        mode="NULL";
        prev_mode_Centri=false;
        mode_using=false;
      }
      if(mode_Follow == false && prev_mode_Follow== false && mode_using==false ){
        mode="Follow";
        prev_mode_Follow=true;
        mode_using=true;
        }

      if(mode_Follow == true && prev_mode_Follow== true && mode_using==true){
        mode="NULL";
        prev_mode_Follow=false;
        mode_using=false;
      }
      if(mode_Scout == false && prev_mode_Scout== false && mode_using==false ){
        mode="Scout";
        prev_mode_Scout=true;
        mode_using=true;
        }

      if(mode_Scout == true && prev_mode_Scout== true && mode_using==true){
        mode="NULL";
        prev_mode_Scout=false;
        mode_using=false;
      }
      
        vTaskDelay(300 / portTICK_PERIOD_MS);  // Add a delay to prevent watchdog
    }
}

//Joystick mode
void task3(void *pvParameters) {
    while (1) {

      if(mode=="Scout"){
//joystick 1 X axis
        if(analogVal_J1X > ADC_HIGH && prev_analogVal_J1X==false && joystick_mode==false){
          joystick_mode_sent="AForward";
          prev_analogVal_J1X=true;
          joystick_mode=true;
        }
        if(analogVal_J1X < ADC_LOW && prev_analogVal_J1X==false && joystick_mode==false){
          joystick_mode_sent="ABackward";
          prev_analogVal_J1X=true;
          joystick_mode=true;
        }
        if(analogVal_J1X < ADC_HIGH && analogVal_J1X > ADC_LOW  && prev_analogVal_J1X== true && joystick_mode==true){
          joystick_mode_sent="NULL";
          prev_analogVal_J1X=false;
          joystick_mode=false;
        }
//joystick 1 Y axis
        if(analogVal_J1Y > ADC_HIGH && prev_analogVal_J1Y==false && joystick_mode==false){
          joystick_mode_sent="BForward";
          prev_analogVal_J1Y=true;
          joystick_mode=true;
        }
        if(analogVal_J1Y < ADC_LOW && prev_analogVal_J1Y==false && joystick_mode==false){
          joystick_mode_sent="BBackward";
          prev_analogVal_J1Y=true;
          joystick_mode=true;
        }
        if(analogVal_J1Y < ADC_HIGH && analogVal_J1Y > ADC_LOW  && prev_analogVal_J1Y == true && joystick_mode==true){
          joystick_mode_sent="NULL";
          prev_analogVal_J1Y=false;
          joystick_mode=false;
        }
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

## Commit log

2024-11-10 added print function
2024-11-10 updating BOM and pi_I2C
    [Utility_Watch_BOM.xlsx]
2024-11-10 Schematic Design
2024-11-10 adding BOM
    [PoC_BotBOM.xlsx, Utility_RemoteBOM.xlsx, Utility_Watch_BOM.xlsx]
2024-11-10 updated schematic V2
2024-11-10 updating Pcb-design
    [Remote_V1.kicad_pcb, Remote_V1.kicad_sch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]
2024-11-11 updating watch_v3 & remote_v2
    [Watch_v3.kicad_pcb, Watch_v3.kicad_sch, remote_v2.kicad_pcb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]
